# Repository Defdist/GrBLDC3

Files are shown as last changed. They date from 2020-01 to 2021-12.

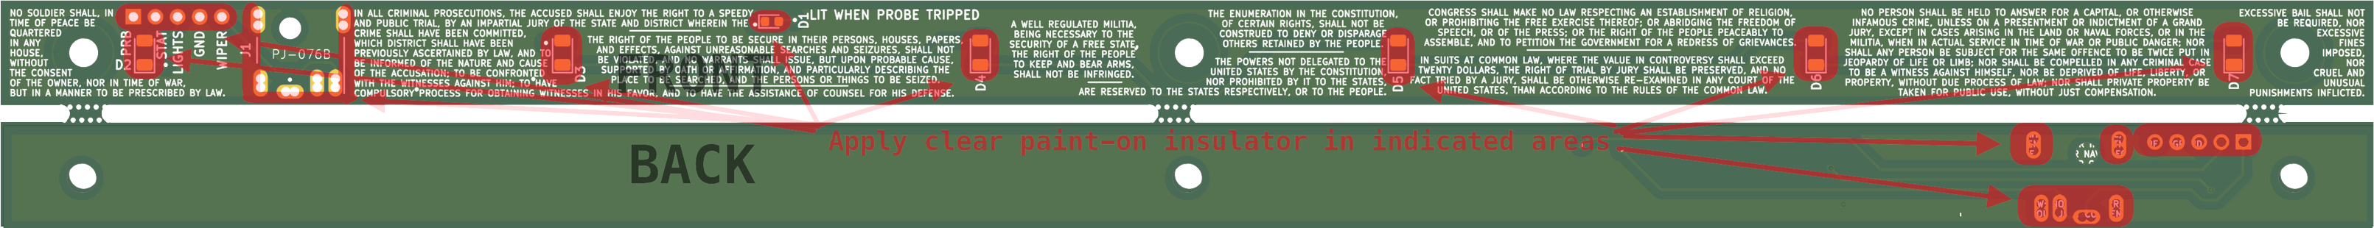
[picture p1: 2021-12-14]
LEDIO PCB/LEDIO 1.2/Areas to Insulate.png

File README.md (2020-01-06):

# GrBLDC3
Uno Shield for grblDD: closed loop spindle VFD + 4 stepper drivers

Main Controller PCB for GG3.  Hardware version 3B
This is the 1st PCB shipped in GG3.

PCB designed in KiCAD.

Changes (from the previous prototype PCB):

-3-pin header order changed from VGS to VSG (e.g. from +-X to +X-).  This creates an incompatibility issue with GG2 units, which will require a pin swap.

-Removed Door Switch (which also restored previous gap for zip tie).

-Vref changed to 1.78 volts (added 1k series with pulldown).

-Added two additional stepper power modes, to reduce power consumption at idle, and to (briefly) increase power if X axis is binding, or if BLDC controller is bogged down in a corner.

-Stepper X1 is now disabled unless A0_STEP_X1_EN is pulled high... this pin is shared with 64M1 reset, which means that when the X1 stepper (only) is disabled, the spindle will not spin.

-Replaced 2x1 screw terminal probe connector with 5x1 SIP.  This is now the only wire harness that goes to LED PCB.  24V and 5V are current limited on this PCB, so that metal chips contacting LED PCB don't affect GrBLDC.

-Added Zener protection diode to 5V rail, in the hope that if 24V finds its way onto that rail, the zener will short it out... this will of course burn out the zener, but hopefully by then the PTC on the Uno will have opened.

-Fixed incorrect pinout on A4910 (pins 39 & 40 swapped).

-BLDC Hall connector changed from 1x5 to 2x3, to make assembling easier.  6th pin is now connected to spindle wipers.

-Removed 2x3 64M1 programming header; connected SPI to Arduino pins instead.  328p can now program this part in-situ (via temporarily loading SPI bitbang firmware onto 328p).

-Emergency stop now pulls BLDC and stepper drivers into reset.

-Emergency stop interface to 328p fixed, such that computer can now pulse reset line during firmware updates.  When estop enabled, 328p continuously held in reset.

-Z stepper connector changed to 2x2, so that it fits through gantry bushings.

-24V/GND/GND 45 degree connector now fits (moved fan connector and capacitors).

New Parts:  
LED PCB:  
102-5777-ND  
Get longer right angle SIPs for LED PCB  
LED - 732-5660-1-ND

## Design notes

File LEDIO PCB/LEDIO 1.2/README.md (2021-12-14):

# LEDIO
LED PCB for GG3.

PCB designed in KiCAD.

Changes (from the previous PCB):

Added fiducials for P&P Camera

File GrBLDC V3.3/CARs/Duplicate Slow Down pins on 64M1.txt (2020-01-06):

Pins PC3 (64M1:7) AND PD4 (64M1:12) perform the same function: tell 328p when to slow down.  This doesn't require a board spin, but if the board is ever modified and more pins are needed, then we can repurpose PC3 (NOT PD4).  PD4 must remain connected because it is the 64M1's SPI programming clock pin.

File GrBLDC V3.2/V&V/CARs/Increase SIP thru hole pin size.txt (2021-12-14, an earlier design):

The thru holes for several SIPs are too small... hard to insert pins.

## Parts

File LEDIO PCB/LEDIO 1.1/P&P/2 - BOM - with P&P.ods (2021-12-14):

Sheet: SMT P&P (ONLY)
Note: This is the master page. The next tab should have columns A:J copy-pasted to create csv file
# | Nozzle | Reel | X p&p | Y p&p | Rot p&p | Height | Skip | Ref | Note | Package | Val | X kicad | Y kicad | Rot kicad | Note | Digikey PN | $@QTY | QTY/GG | QTY in 700 GG3s | nominal $ per GG3 | Leftover QTY from GG2 | QTY needed for 700 GG3s | purchased in multiples of | QTY to buy in 1st order | $ (total)
 |  |  |  |  |  |  |  |  |  |  |  |  |  |  |  |  |  |  | $(nom)/PCB | #REF!

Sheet: Hand Place (ONLY)
Description | Note | Digikey PN | $@QTY | QTY/GG | QTY in 700 GG3s | nominal $ per GG3 | Leftover QTY from GG2 | QTY needed for 700 GG3s | purchased in multiples of | QTY to buy in 1st order | $ (total) in 1st order
Barrel Jack |  | PJ-076B | 0.5808 | 1 | 700 | 0.58 | 0 | 700 | 1000 | 1000 | 580.8
Barrel Connector | Technically part of probe cable, but included here | CP3-1001-ND | 0.7136 | 1 | 700 | 0.71 | 0 | 700 | 1000 | 1000 | 713.6
Right angle conn | 0.015 uin min gold plating, 8 to 9 mm length | WM50026-05-ND | 0.2520 | 1 | 700 | 0.25 | 0 | 700 | 500 | 700 | 176.37
LED - green | Right angle | 160-1478-1-ND | 0.0432 | 1 | 700 | 0.04 | 0 | 700 | 4000 | 4000 | 172.96
LED - white |  | 732-5660-2-ND | 0.1330 | 6 | 4200 | 0.8 | 6000 | -1800 | 2000 | 0 | 0
LED PCB | The actual PCB | - | 0.5400 | 1 | 700 | 0.54 | 0 | 700 | 500 | 1000 | 540
 |  |  |  |  | $(nom)/PCB | 2.93

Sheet: FULL BOM EXPORT
Part | Note | Digikey PN | $@QTY | QTY /GG | QTY in 700 GG3s | nominal $ per GG3 | Leftover GG2 QTY | QTY needed for 700 GG3s | purchased in multiples of | Recommended QTY to buy in 1st order | $ for 1st order
 |  |  |  |  | nominal $ per GG3 | #REF!

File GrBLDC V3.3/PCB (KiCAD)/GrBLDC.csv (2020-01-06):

Id | Designator | Package | Quantity | Designation | Supplier and ref
1 | Fiducial,Fiducial,Fiducial | Fiducial | 3 | VAL**
2 | C6,C36,C37,C29,C21,C35,C38,C48,C49,C50,C51,C53,C52,C44 | SM1206 | 14 | 10u
3 | C7,C25,C20,C16,C24,C5,C3,C4 | SM0805 | 8 | 1u
4 | R32,R29,R31,R34,R33,R30 | SM0603 | 6 | 470k
5 | R28,R27,R26,R25,R24,R23,R51,R52 | SM0603 | 8 | 47
6 | C2,C28,C22,C19,C26,C23,C14,C10,C11,C8,C12,C9,C15,C1,C17,C27,C34,C39,C18,C42,C13 | SM0603 | 21 | 220n
7 | R2,R1,R4,R47,R45,R44,R42 | SM0603 | 7 | 470
8 | C31,C32,C30 | SM0603 | 3 | 33n
9 | R20,R5,R6,R18,R19,R21,R7,R37 | SM0603 | 8 | 40.2k
10 | R16,R13,R14,R10,R15,R11,R12,R8,R9,R3,R22,R36,R35,R43,R46,R48,R50 | SM0603 | 17 | 1k
11 | P5 | SIL-9 | 1 | CONN_9
12 | P10,P2,P6,P9,P7,P4 | SIL-8 | 6 | CONN_8
13 | P1 | SIL-6 | 1 | CONN_6
14 | JP1 | SIL-3 | 1 | JUMPER3
15 | P11 | SIL-2 | 1 | CONN_2
16 | P12 | Conn_1751280 | 1 | CONN_6
17 | C33,C46,C43 | Cap_Nichicon_UCL1V331MNL1GS | 3 | 330u
18 | C45,C47 | Cap_Nichicon_UCL1V331MNL1GS | 2 | 220u
19 | U1 | A4915 | 1 | A4915-JTS
20 | P8,P3 | Conn_1751303 | 2 | CONN_8
21 | ILTC1 | ILTC | 1 | ILTC
22 | R17,R40 | SM0603 | 2 | SPARE
23 | VAL | DDsmall | 1 | REF
24 | U4 | SOT23-5 | 1 | LT1797
25 | U3,U2 | SOT23-5 | 2 | MCP6561
26 | D1 | SOT23 | 1 | LM4040
27 | R49 | SM1206 | 1 | 0.010
28 | C41 | SM1206 | 1 | 82n
29 | R39,R38,R41 | SM0603 | 3 | 40.2K
30 | C40 | SM0603 | 1 | 2n
31 | RV1 | POT_3361 | 1 | POT
32 | Q5,Q4,Q6,Q3,Q2,Q1 | IRF5406 | 6 | IRF5406

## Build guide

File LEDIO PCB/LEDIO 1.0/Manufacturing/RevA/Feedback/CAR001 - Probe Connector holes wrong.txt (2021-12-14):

DC Power jack connector PTH incorrect... jack leads don't fit through (round) hole.
Headphone jack connector PTH incorrect... jack leads don't fit through (round) hole.

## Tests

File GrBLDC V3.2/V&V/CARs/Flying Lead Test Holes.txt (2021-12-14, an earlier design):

Need to add flying lead test holes so that Seeedstudio doesn't blow holes through planes in bad places.

Seeed recommends:
1.5 mm min, preferably 2 mm
one hole on each corner
Fixture testing (large batches) requires board margins

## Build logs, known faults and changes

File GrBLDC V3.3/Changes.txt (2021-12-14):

RevC Changes:

-Added QTY4 mechanical thru holes for flying probe tester
-Added D4 to prevent sinking into the 24 volt rail.  PN is SMZJ3800B-E3/52GITR-ND
-Changed Thru hole ID on P1/P2/P8/P9/P10/P11 from 0.813 mm to 1.000 mm
-Moved C51/C55/C56/C59/C60 to make room for D4.

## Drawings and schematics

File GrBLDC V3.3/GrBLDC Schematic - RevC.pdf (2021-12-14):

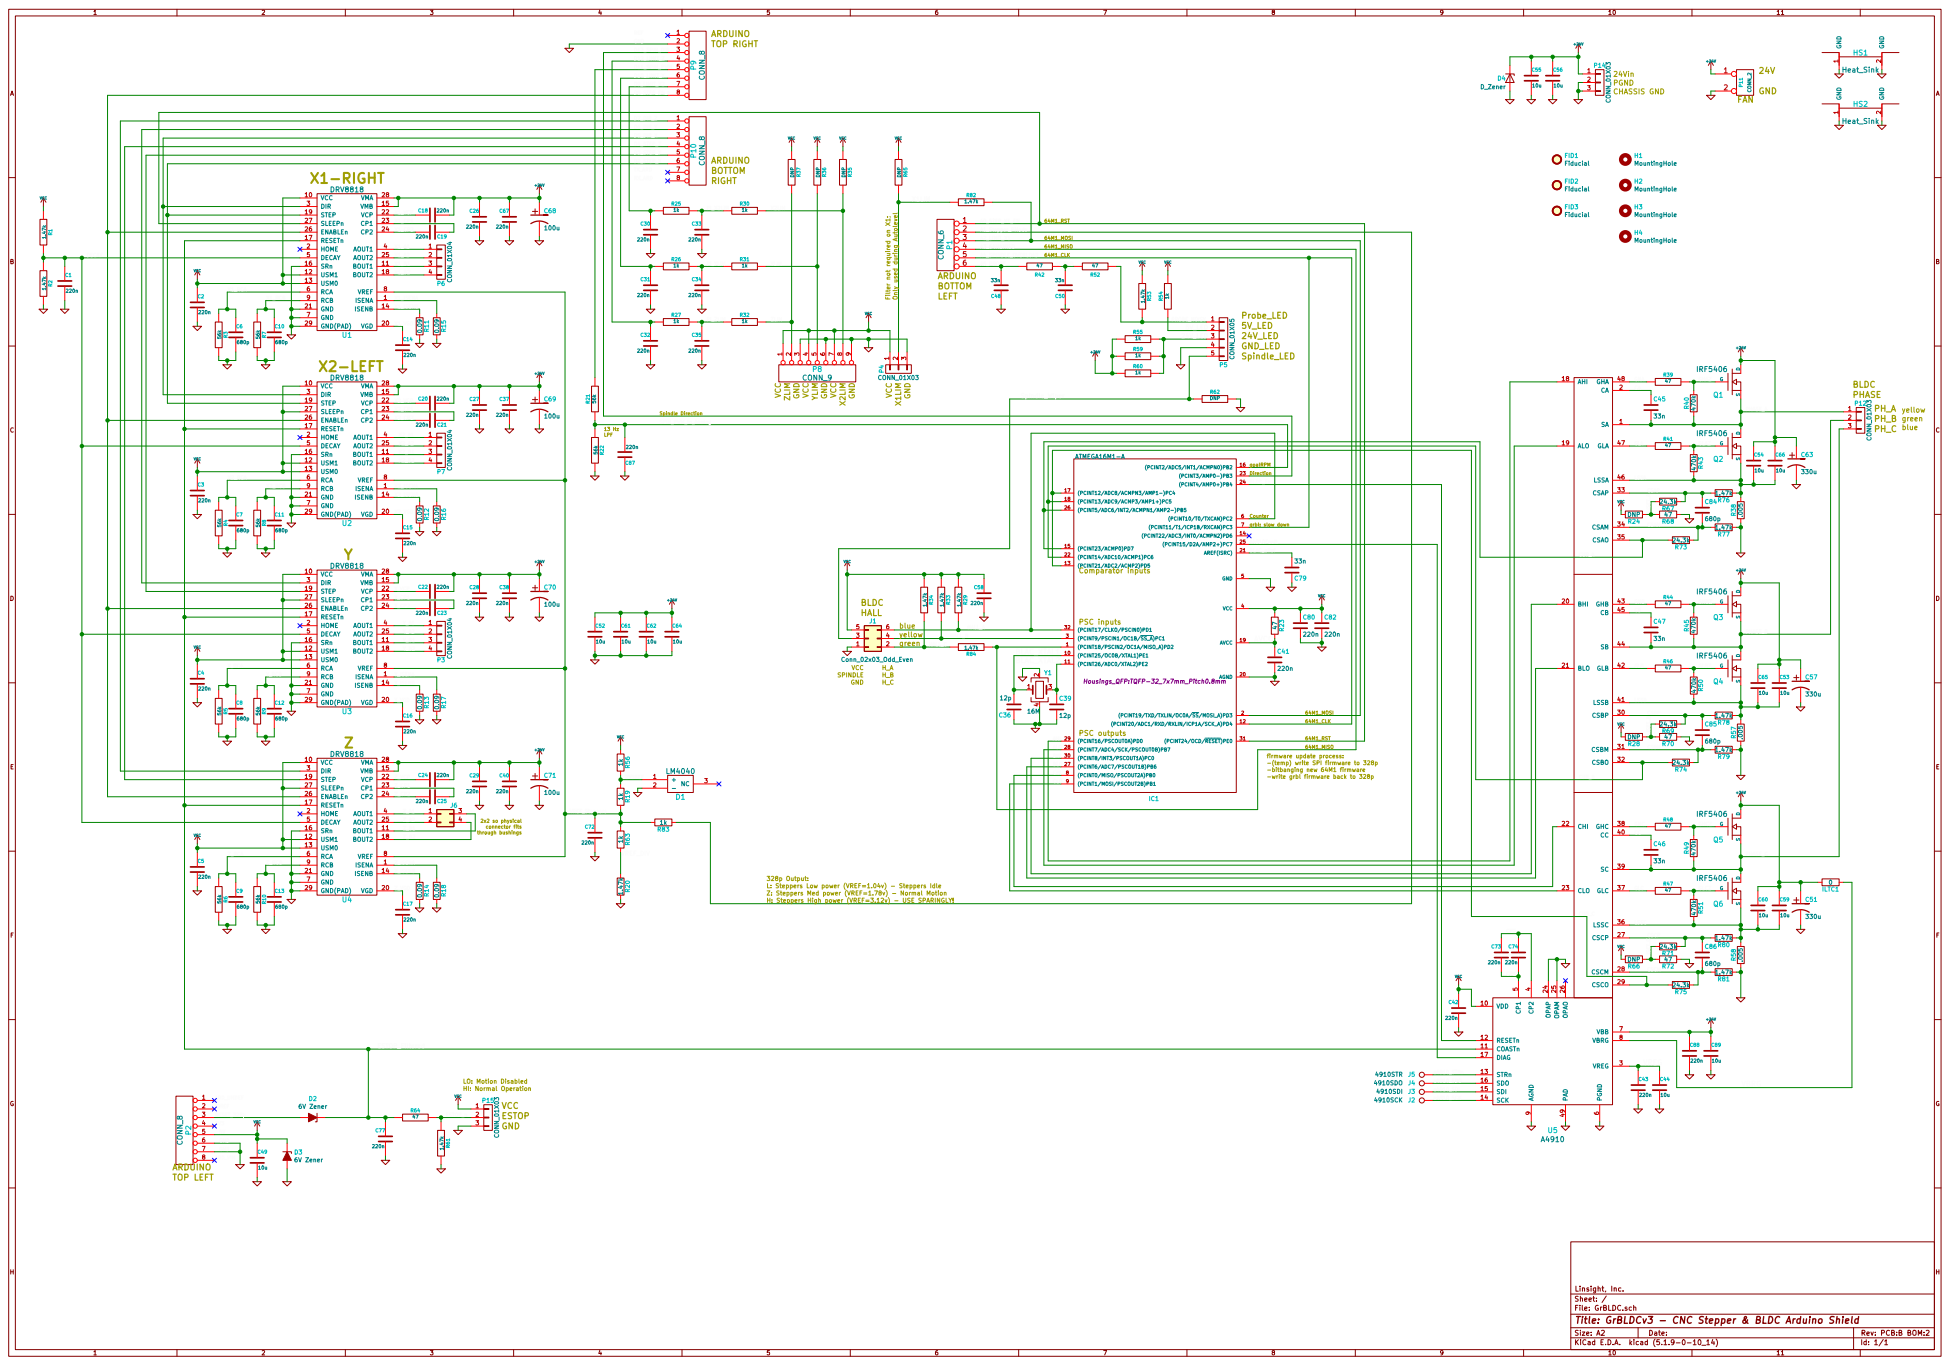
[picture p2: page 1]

goalRPM VCC ZLIM GND VCC YLIM GND VCC X2LIM GND

firmware update process:
-(temp) write SPI firmware to 328p -bitbanging new 64M1 firmware

-write grbl firmware back to 328p

2x2 so physical connector fits

328p Output:
L: Steppers Low power (VREF=1.04v) - Steppers Idle
Z: Steppers Med power (VREF=1.78v) - Normal Motion
H: Steppers High power (VREF=3.12v) - USE SPARINGLY!

File: GrBLDC.sch Sheet: / Linsight, Inc.

Id: 1/1 Title: GrBLDCv3 - CNC Stepper & BLDC Arduino Shield

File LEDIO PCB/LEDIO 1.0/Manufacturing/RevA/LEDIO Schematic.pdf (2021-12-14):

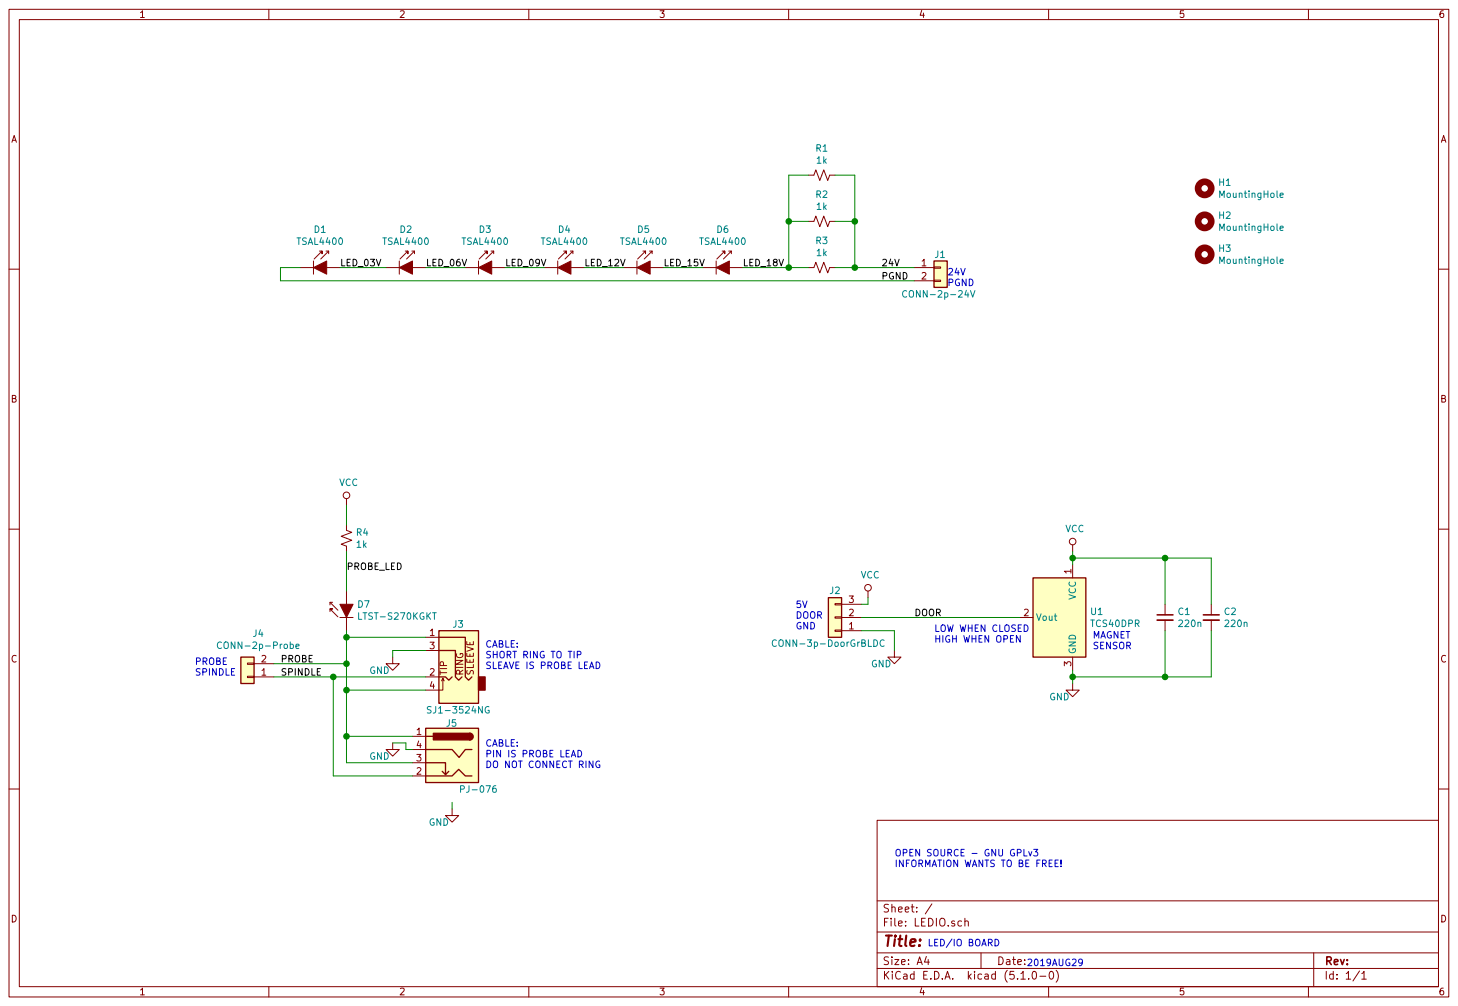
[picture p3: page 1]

J2 CONN-3p-DoorGrBLDC TIP RING SLEEVE

DOOR
INFORMATION WANTS TO BE FREE! LOW WHEN CLOSED

SLEAVE IS PROBE LEAD

CABLE: PIN IS PROBE LEAD

DO NOT CONNECT RING

LED/IO BOARD OPEN SOURCE - GNU GPLv3

Id: 1/1 Title: File: LEDIO.sch Sheet: /

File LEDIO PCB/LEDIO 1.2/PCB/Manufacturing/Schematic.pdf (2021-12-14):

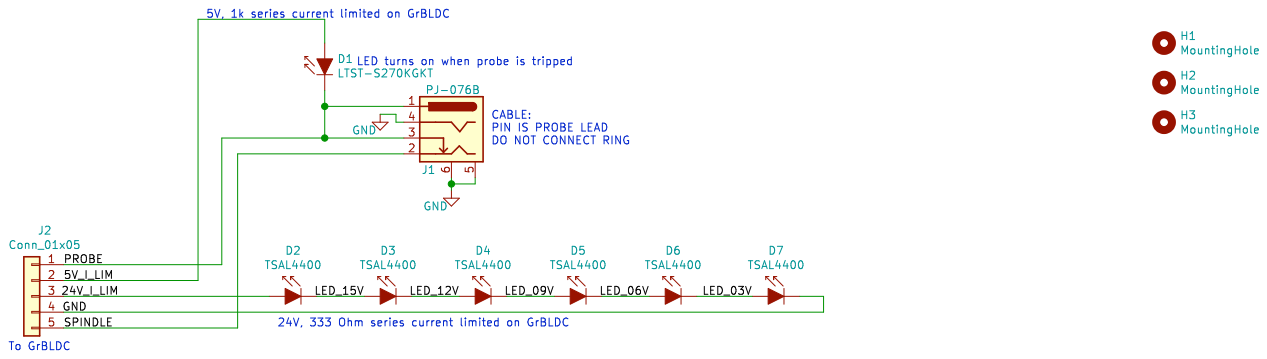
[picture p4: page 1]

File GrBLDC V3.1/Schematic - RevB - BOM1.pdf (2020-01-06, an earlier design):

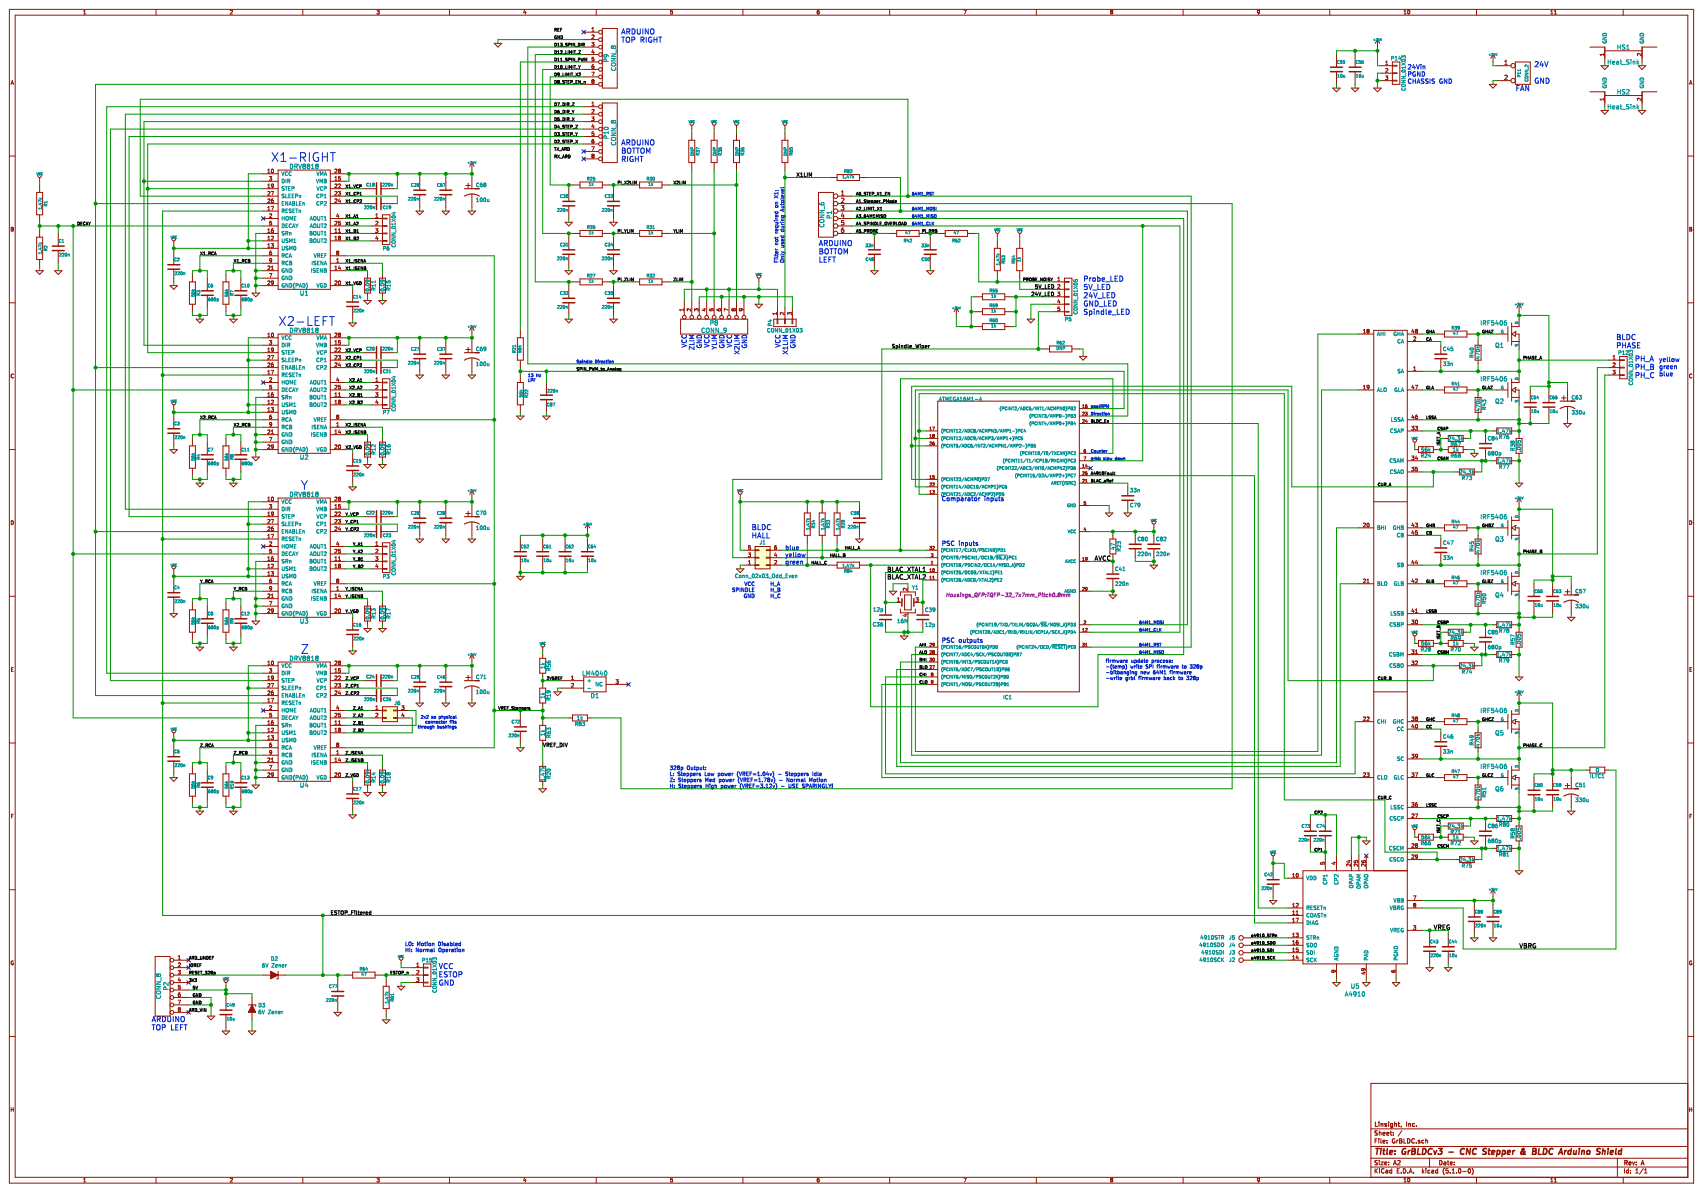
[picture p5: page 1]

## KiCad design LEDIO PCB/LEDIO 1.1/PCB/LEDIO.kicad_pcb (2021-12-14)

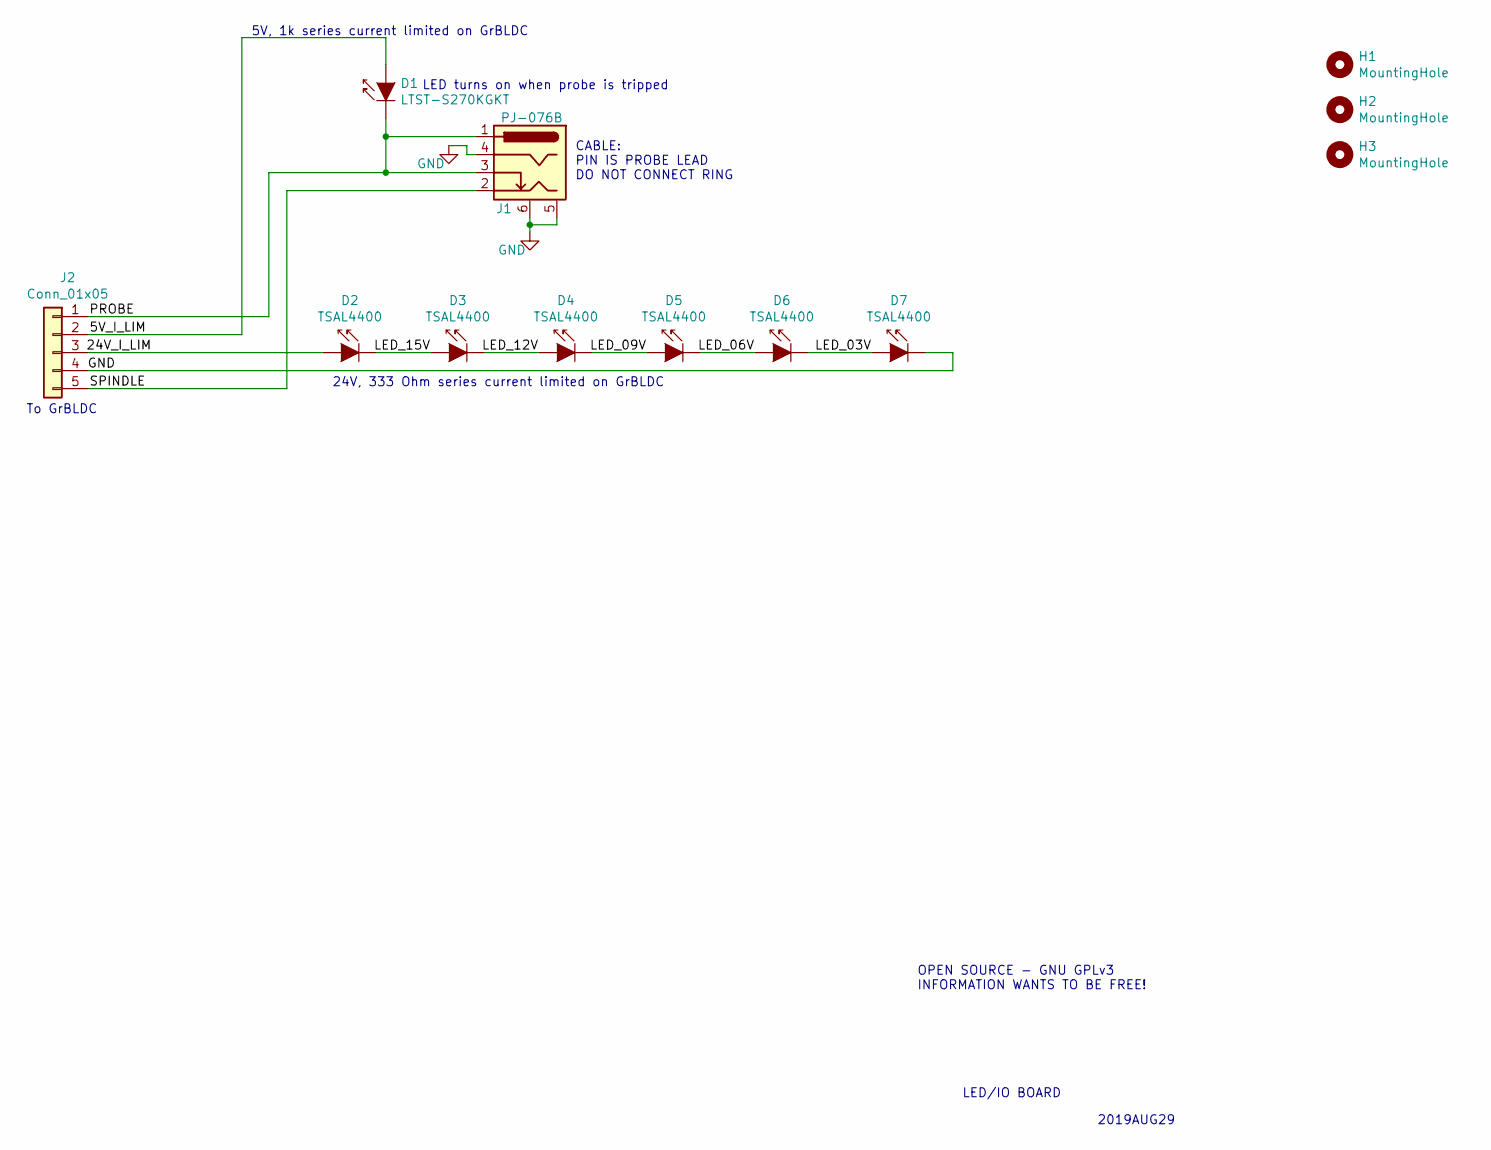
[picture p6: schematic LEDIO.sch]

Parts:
D1: LTST-S270KGKT; D_0603_1608Metric
D2, D3, D4, D5, D6, D7: TSAL4400; D_1206_3216Metric
H1, H2, H3: MountingHole; MountingHole_3.2mm_M3
J1: PJ-076B; CUI_PJ-076
J2: Conn_01x05; PinHeader_1x05_P2.54mm_Horizontal

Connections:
/5V_I_LIM: D1.2 (A), J2.2
/24V_I_LIM: D2.2 (A), J2.3
/LED_03V: D6.1 (K), D7.2 (A)
/LED_06V: D5.1 (K), D6.2 (A)
/LED_09V: D4.1 (K), D5.2 (A)
/LED_12V: D3.1 (K), D4.2 (A)
/LED_15V: D2.1 (K), D3.2 (A)
/PROBE: D1.1 (K), J1.1, J1.3, J2.1
/SPINDLE: J1.2, J2.5
GND: D7.1 (K), J1.4, J1.5 (ShieldA), J1.6 (ShieldB), J2.4

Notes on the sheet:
CABLE: PIN IS PROBE LEAD DO NOT CONNECT RING
2019AUG29
LED/IO BOARD
OPEN SOURCE - GNU GPLv3 INFORMATION WANTS TO BE FREE!
5V, 1k series current limited on GrBLDC
To GrBLDC
LED turns on when probe is tripped
24V, 333 Ohm series current limited on GrBLDC

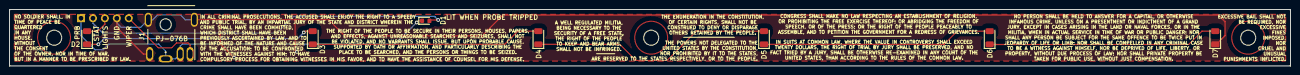
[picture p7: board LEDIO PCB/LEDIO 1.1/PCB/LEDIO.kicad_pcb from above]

Board: 2 copper layers, 272.5 x 12.0 mm, 12 parts (1 on the bottom side), 10 nets.

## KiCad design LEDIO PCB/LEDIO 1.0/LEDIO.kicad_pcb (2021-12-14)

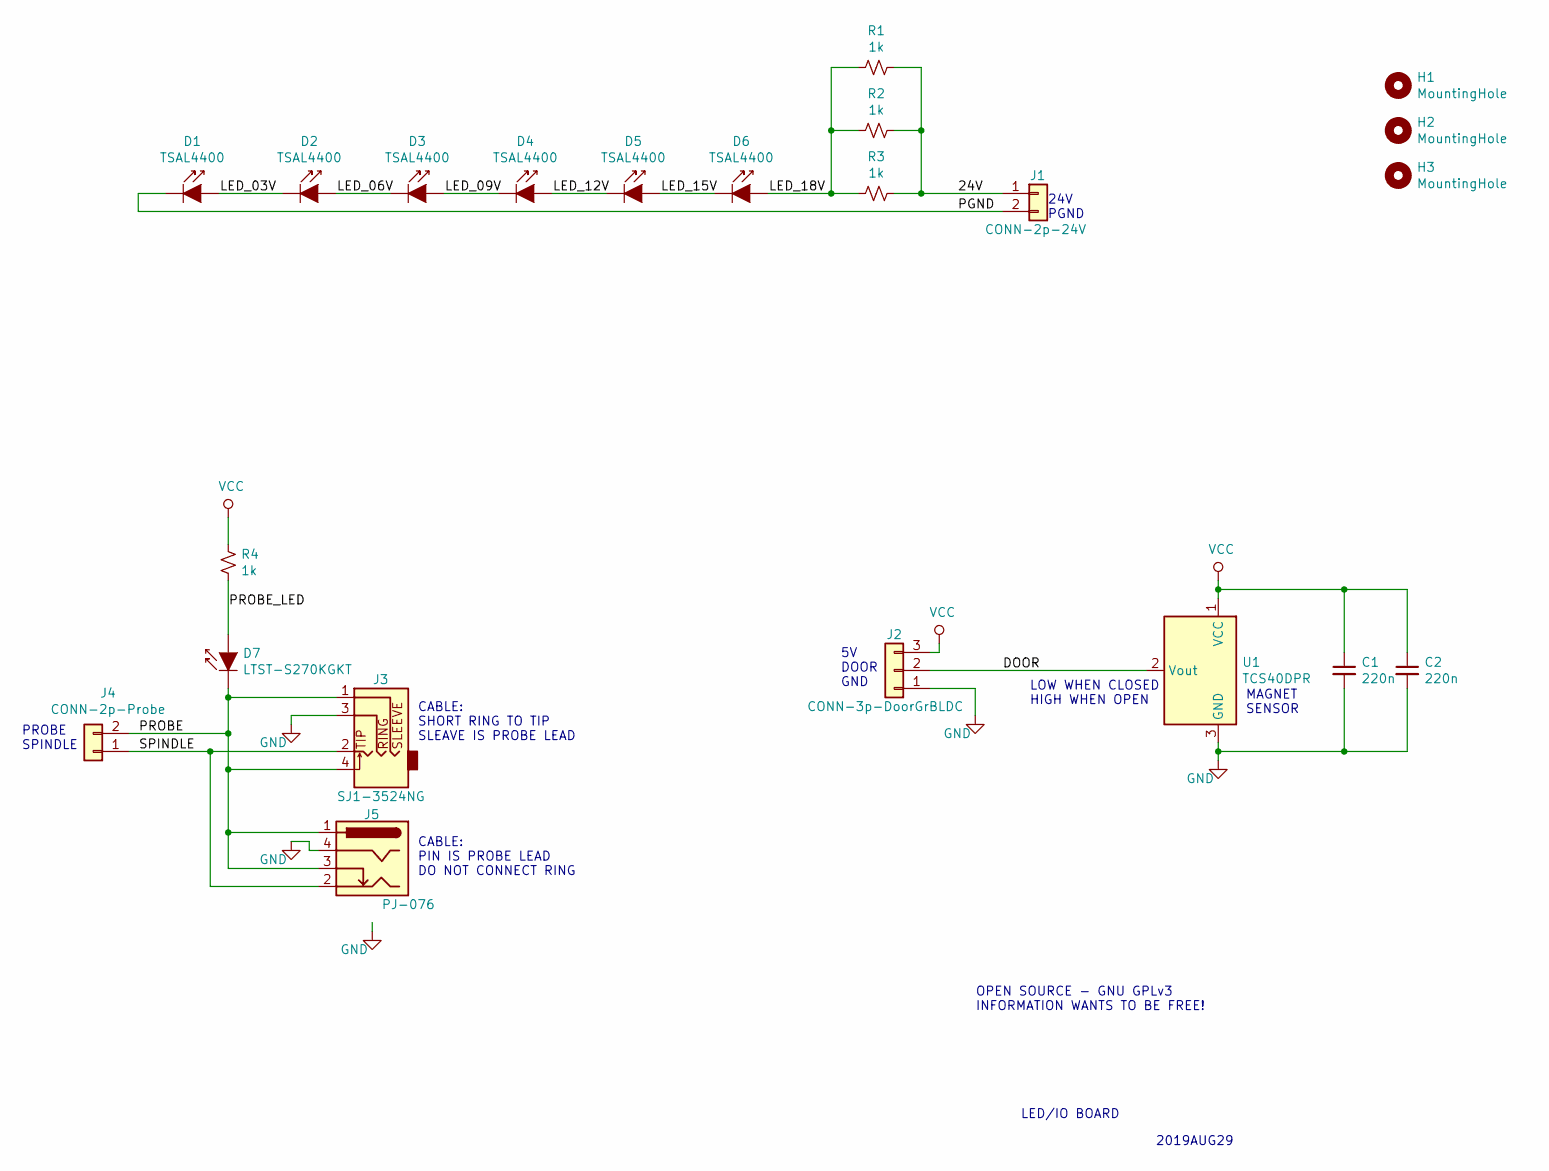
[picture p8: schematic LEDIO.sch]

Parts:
C1, C2: 220n; C_0603_1608Metric
D1, D2, D3, D4, D5, D6: TSAL4400; D_1206_3216Metric
D7: LTST-S270KGKT; D_0603_1608Metric
H1, H2, H3: MountingHole; MountingHole_3.2mm_M3
J1: CONN-2p-24V; PinHeader_1x02_P2.54mm_Horizontal
J2: CONN-3p-DoorGrBLDC; PinHeader_1x03_P2.54mm_Horizontal
J3: SJ1-3524NG; CUI_SJ1-3524NG
J4: CONN-2p-Probe; PinHeader_1x02_P2.54mm_Horizontal
J5: PJ-076; CUI_PJ-076
R1, R2, R3, R4: 1k; R_0603_1608Metric
U1: TCS40DPR; SOT-23

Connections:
/24V: J1.1, R1.1, R2.1, R3.1
/DOOR: J2.2, U1.2 (Vout)
/LED_03V: D1.2 (A), D2.1 (K)
/LED_06V: D2.2 (A), D3.1 (K)
/LED_09V: D3.2 (A), D4.1 (K)
/LED_12V: D4.2 (A), D5.1 (K)
/LED_15V: D5.2 (A), D6.1 (K)
/LED_18V: D6.2 (A), R1.2, R2.2, R3.2
/PGND: D1.1 (K), J1.2
/PROBE: D7.1 (K), J3.1, J3.4, J4.2, J5.1, J5.3
/PROBE_LED: D7.2 (A), R4.2
/SPINDLE: J3.2, J4.1, J5.2
GND: C1.2, C2.2, J2.1, J3.3, J5.4, U1.3 (GND)
VCC: C1.1, C2.1, J2.3, R4.1, U1.1 (VCC)

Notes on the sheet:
24V PGND
5V DOOR GND
PROBE SPINDLE
CABLE: SHORT RING TO TIP SLEAVE IS PROBE LEAD
CABLE: PIN IS PROBE LEAD DO NOT CONNECT RING
MAGNET SENSOR
2019AUG29
LED/IO BOARD
OPEN SOURCE - GNU GPLv3 INFORMATION WANTS TO BE FREE!
LOW WHEN CLOSED HIGH WHEN OPEN

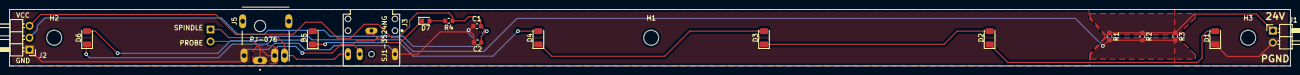
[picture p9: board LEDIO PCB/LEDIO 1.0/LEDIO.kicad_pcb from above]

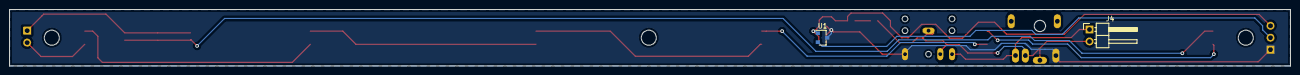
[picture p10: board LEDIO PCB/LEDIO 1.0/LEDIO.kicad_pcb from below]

Board: 2 copper layers, 272.5 x 12.0 mm, 22 parts (2 on the bottom side), 14 nets.

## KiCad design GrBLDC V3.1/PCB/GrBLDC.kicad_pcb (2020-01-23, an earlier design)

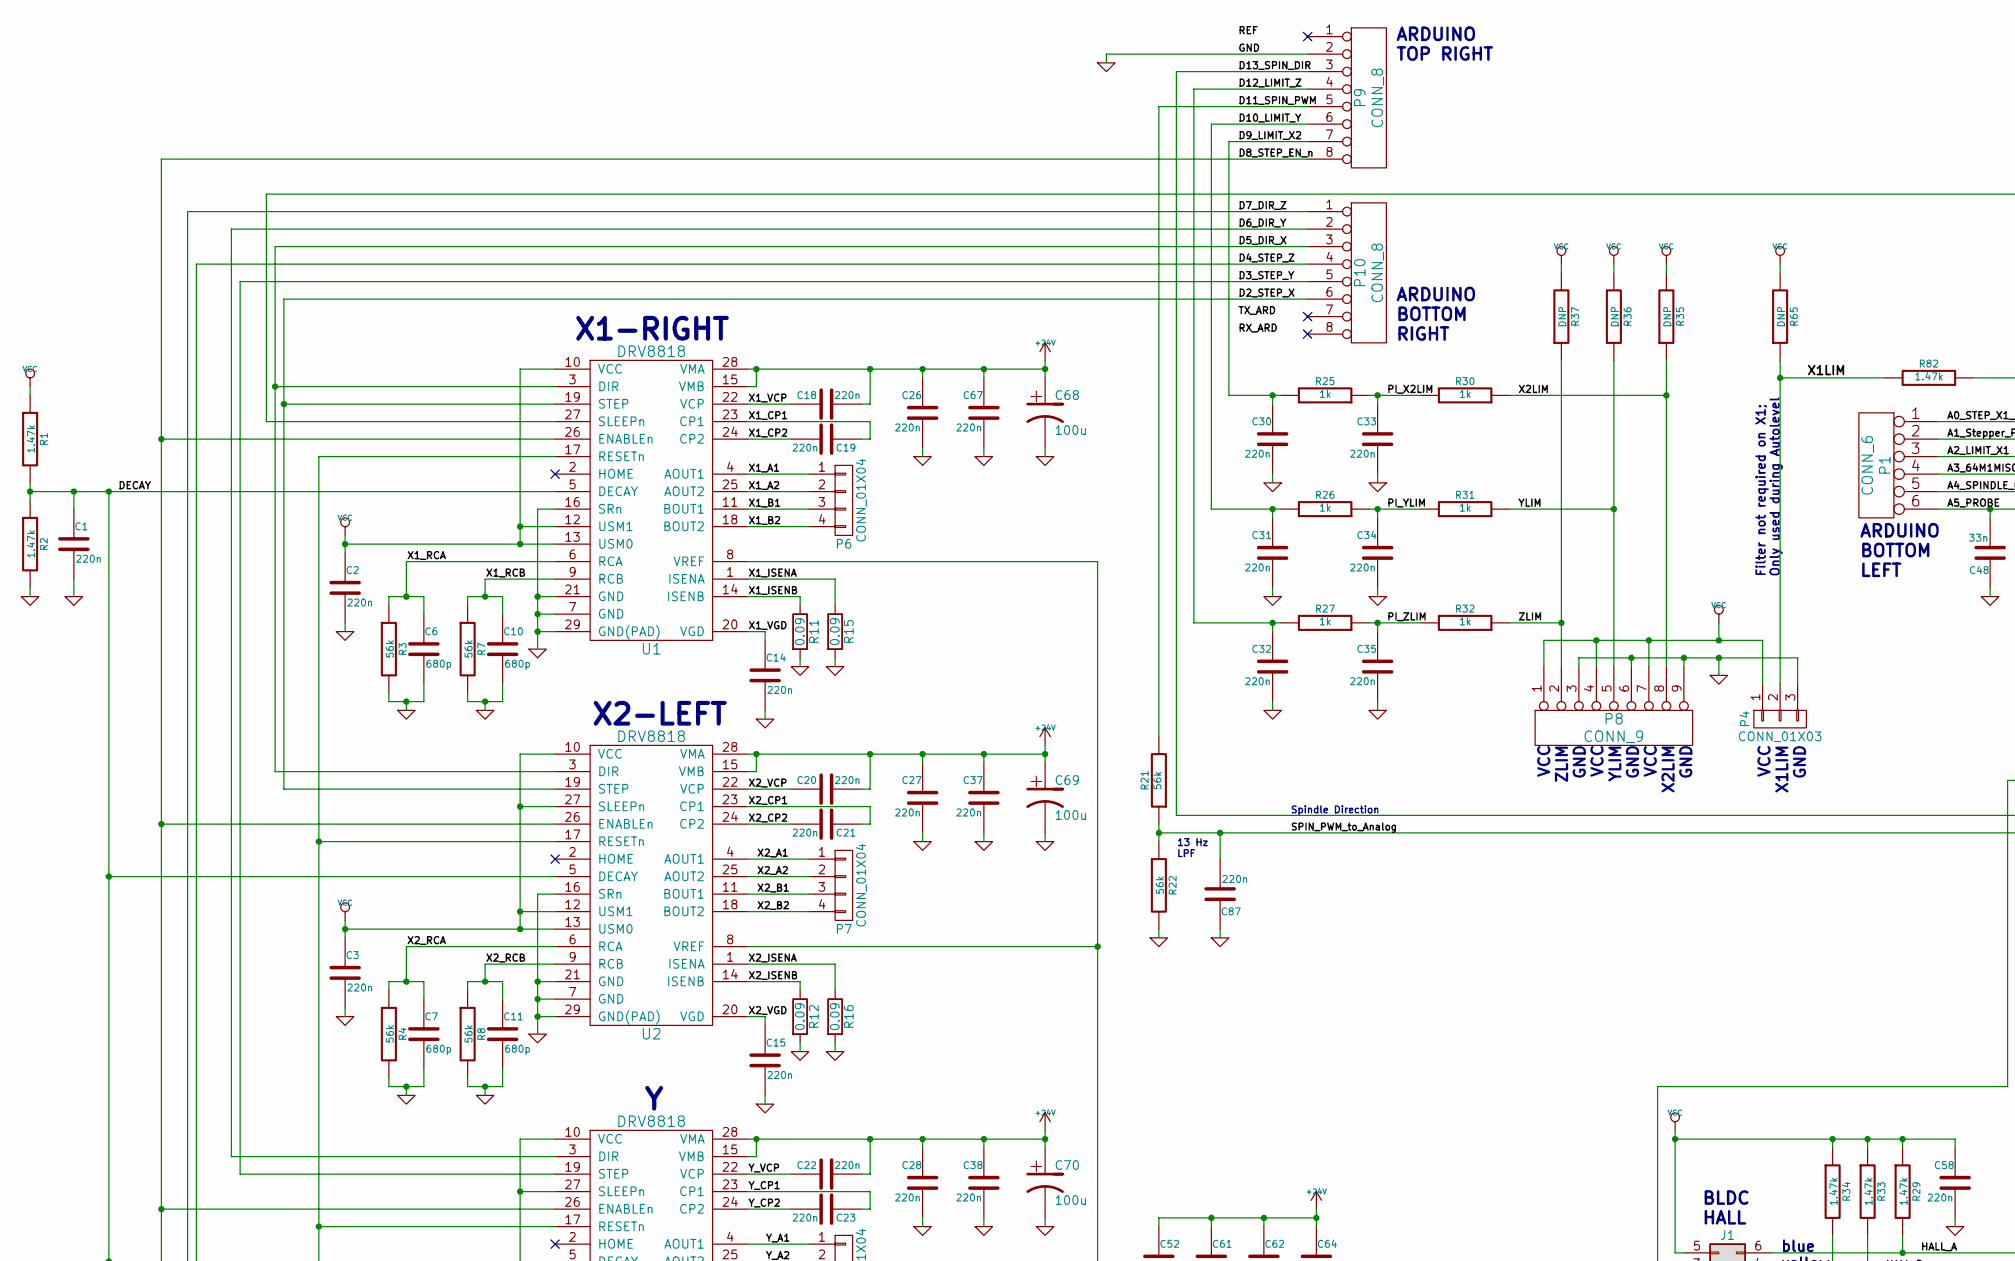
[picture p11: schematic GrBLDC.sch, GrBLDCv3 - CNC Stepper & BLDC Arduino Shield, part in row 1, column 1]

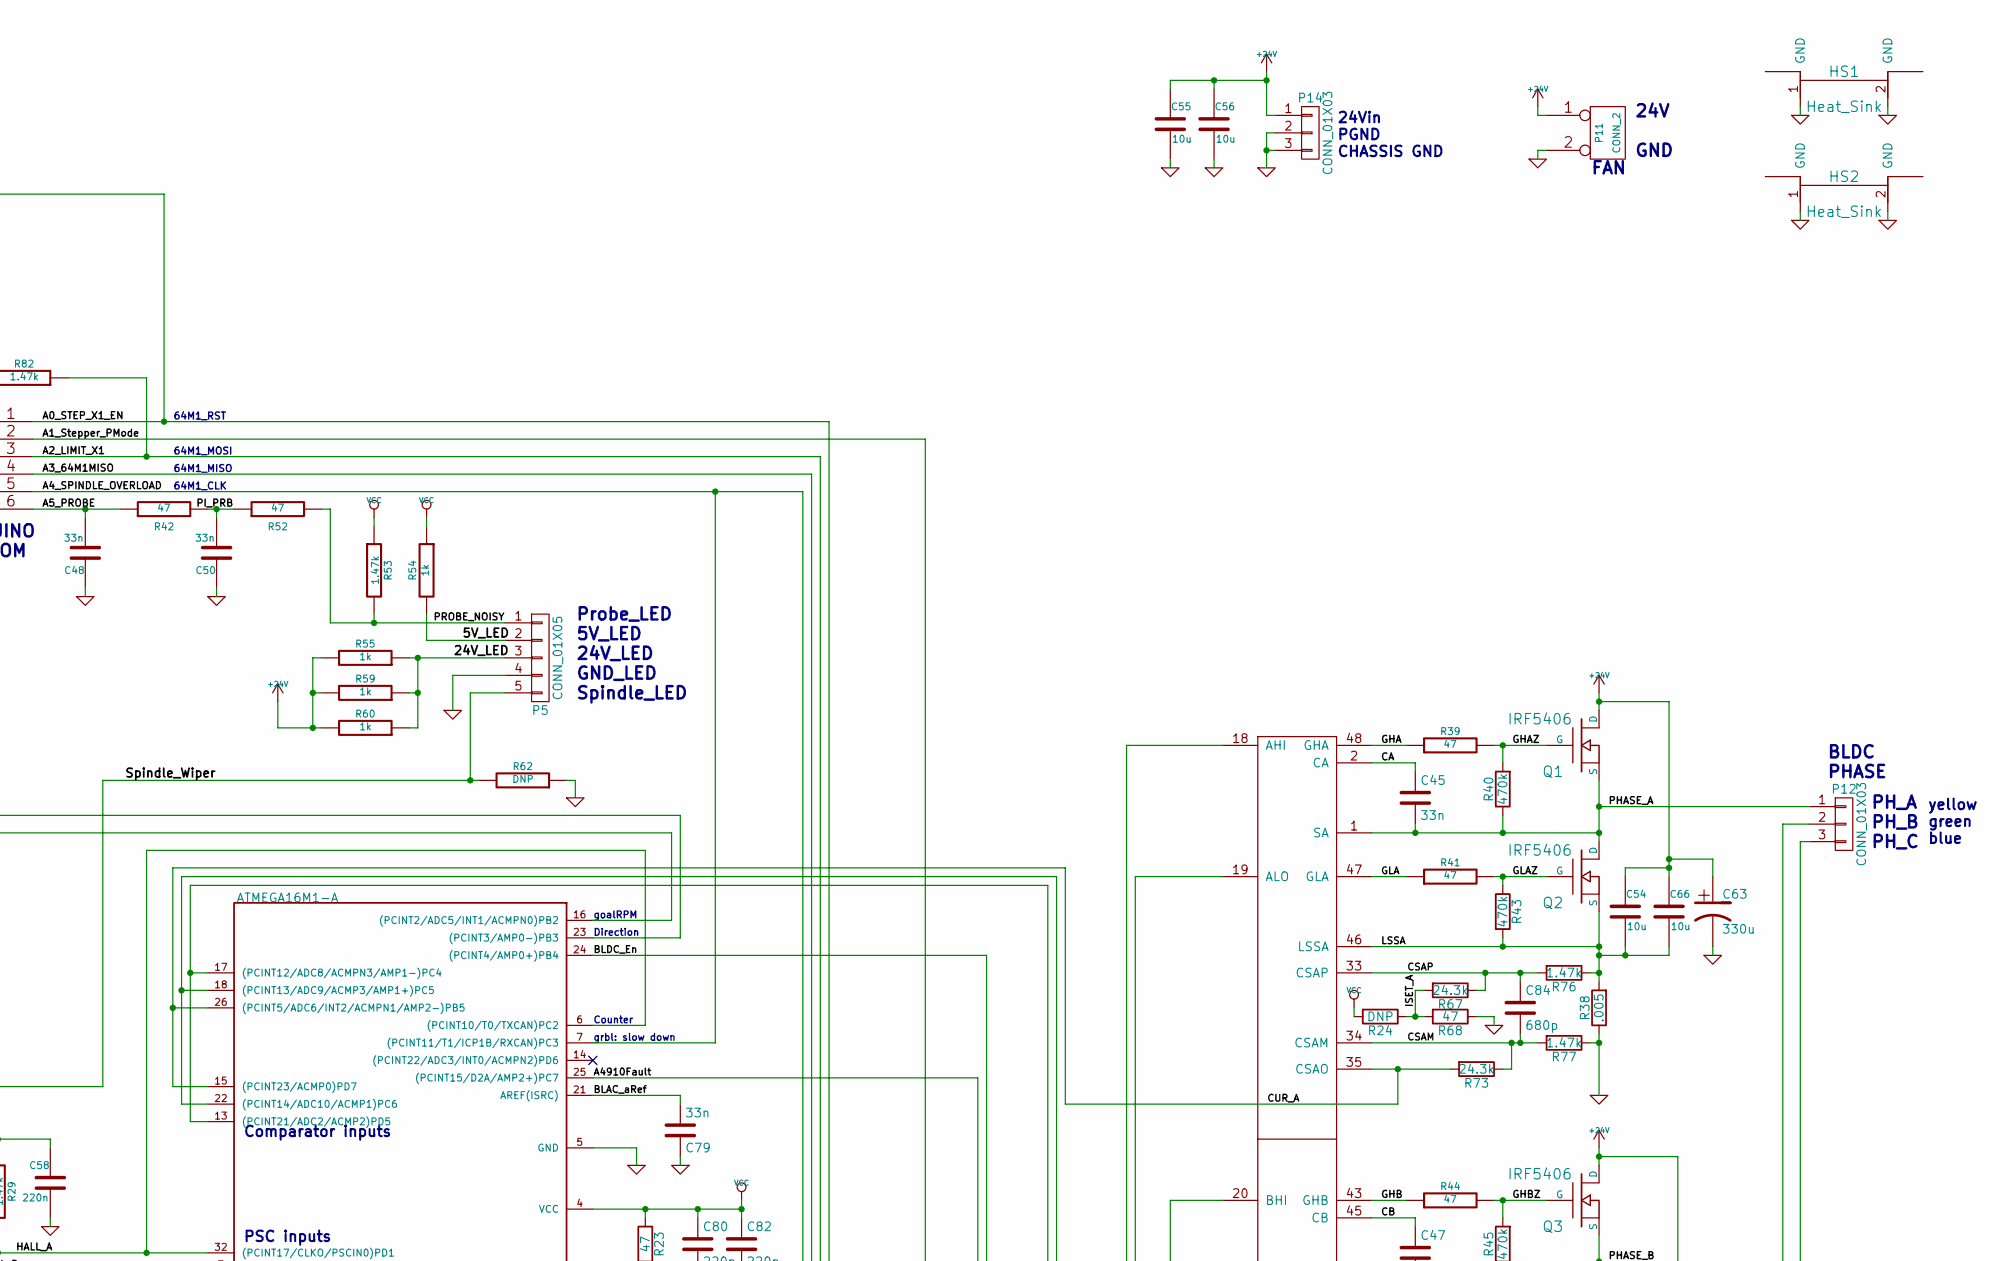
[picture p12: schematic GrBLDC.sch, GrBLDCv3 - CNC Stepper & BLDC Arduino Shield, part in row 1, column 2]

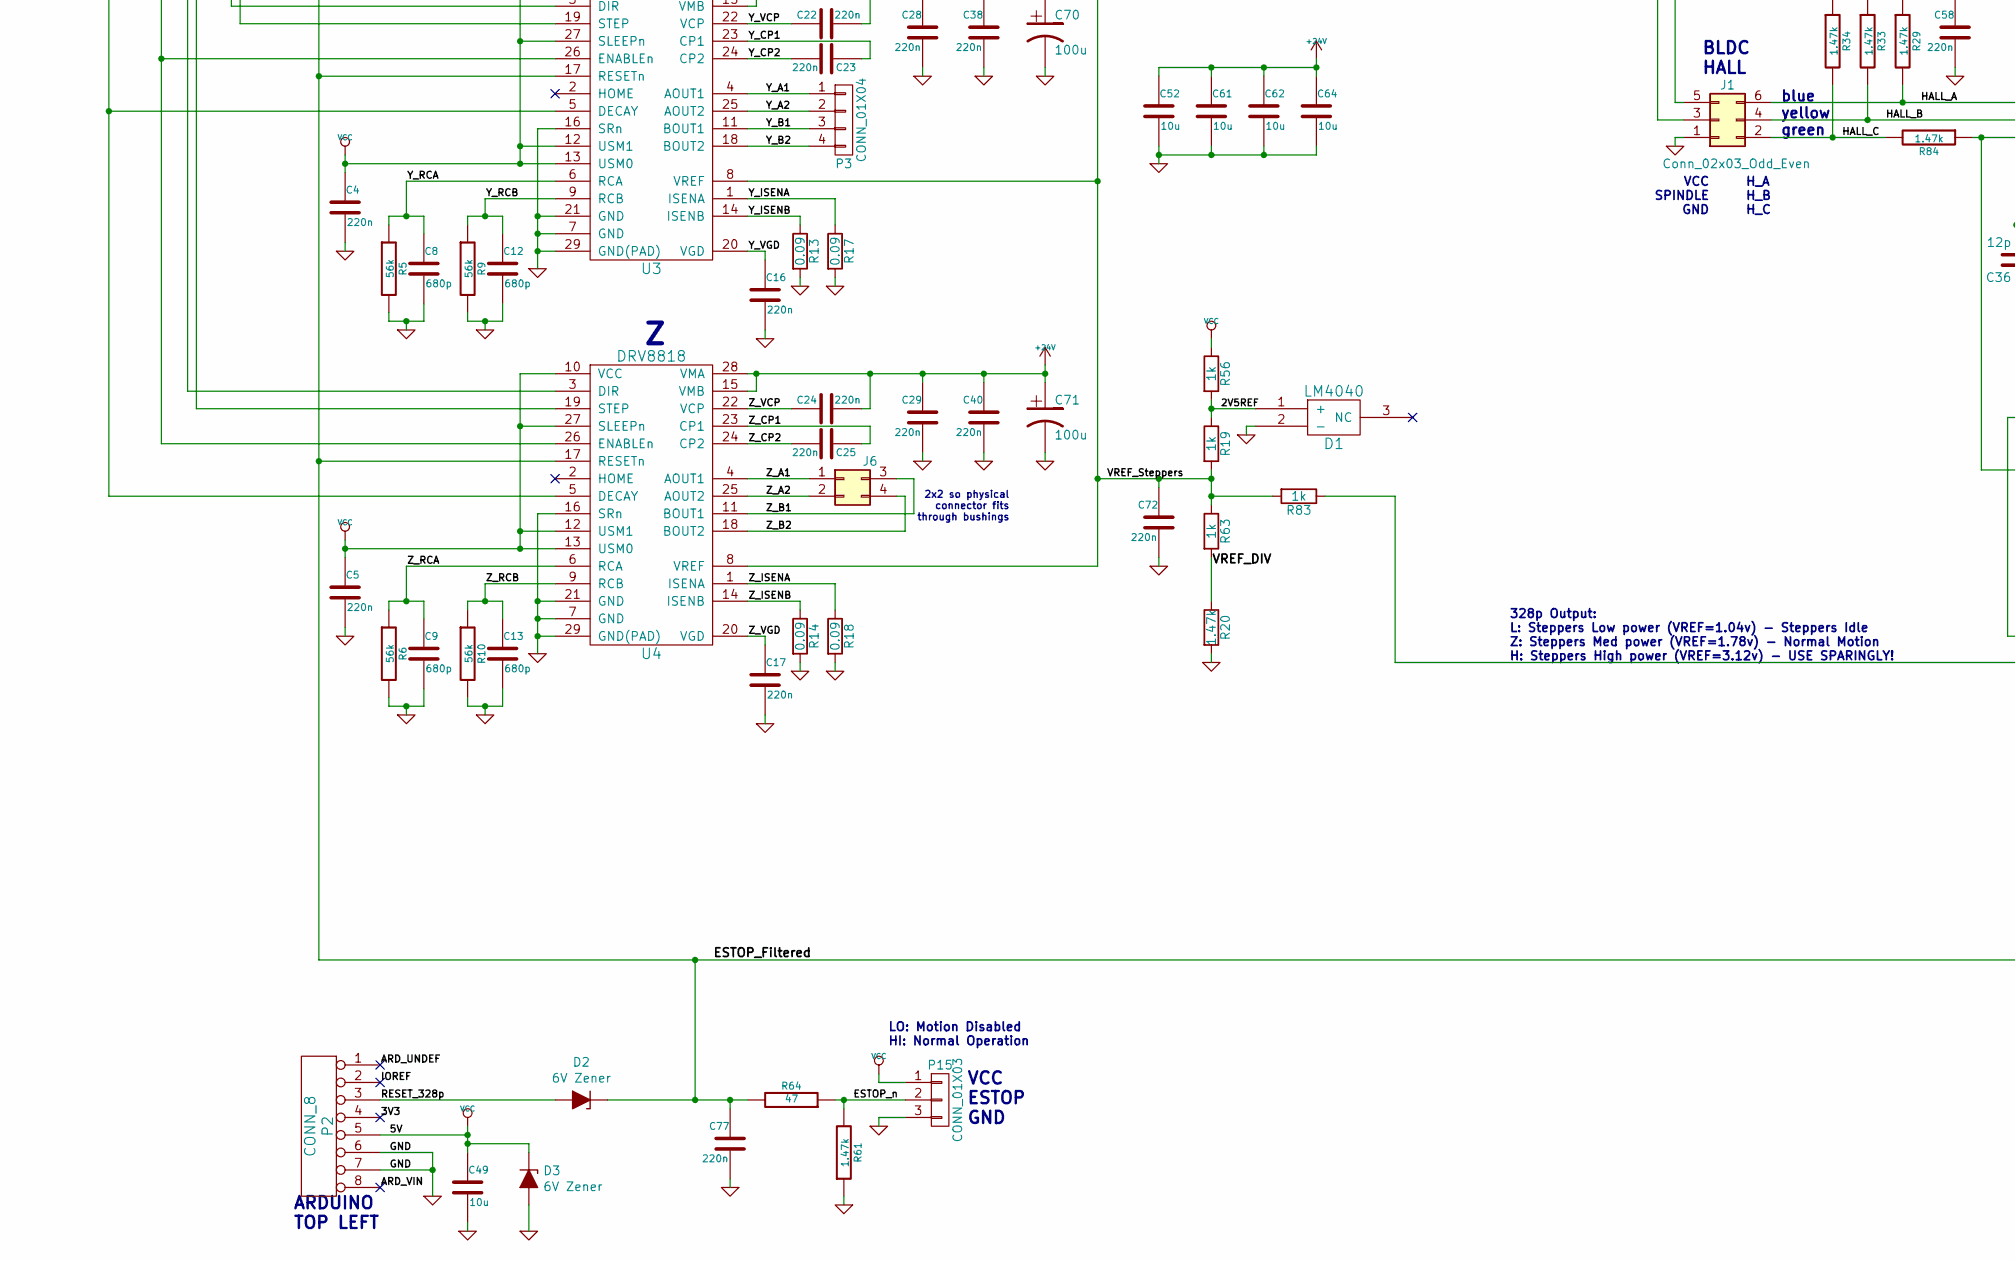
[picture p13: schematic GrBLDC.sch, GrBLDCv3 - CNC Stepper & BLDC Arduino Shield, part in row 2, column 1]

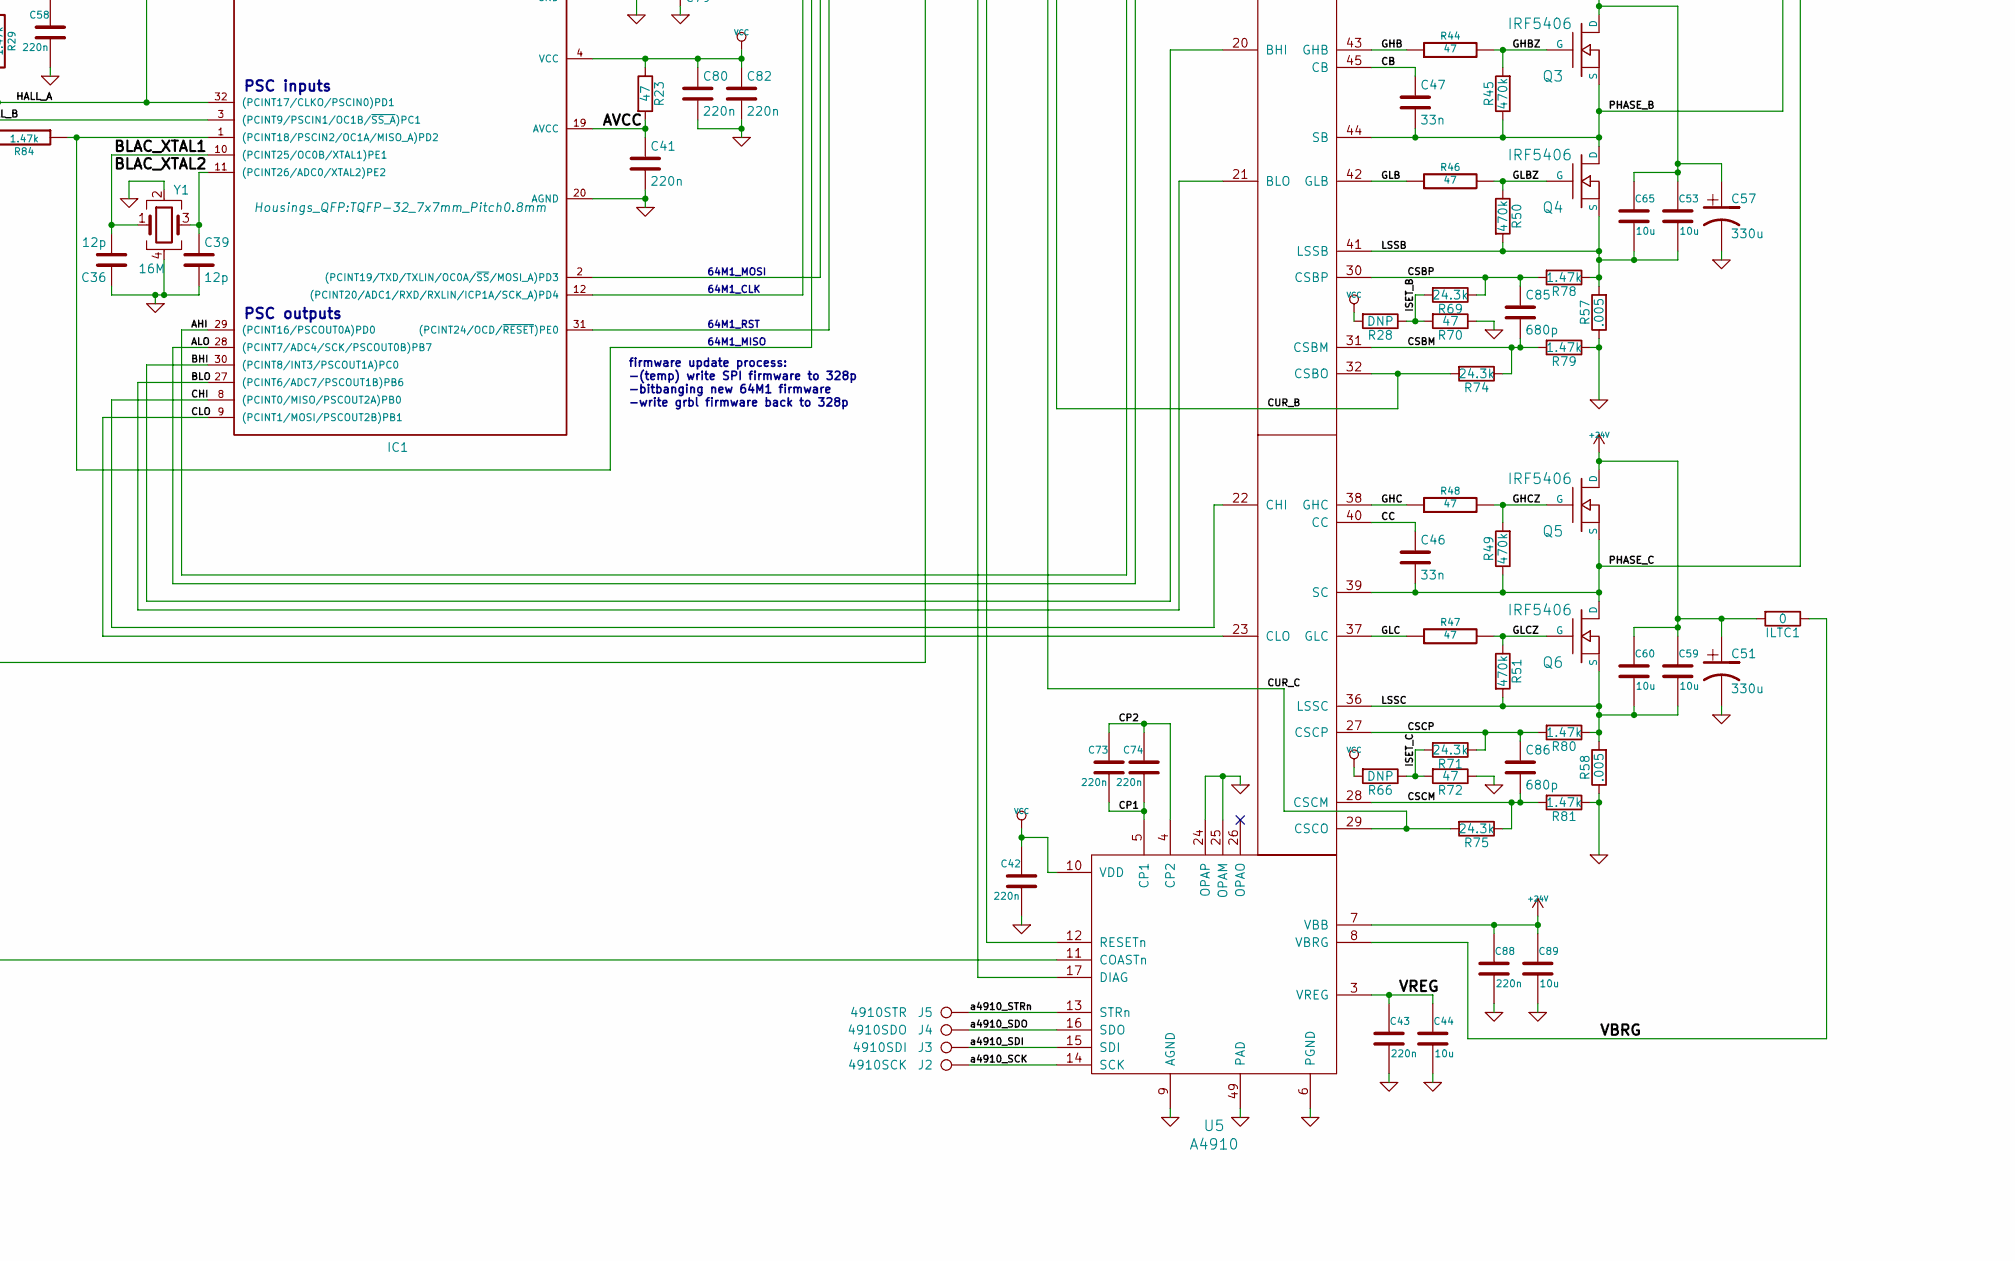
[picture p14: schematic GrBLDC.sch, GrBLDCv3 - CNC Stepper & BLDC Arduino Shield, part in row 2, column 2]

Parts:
C1, C2, C3, C4, C5, C14, C15, C16, C17, C18, C19, C20, C21, C22, C23, C24, C25, C26, C27, C28, C29, C30, C31, C32, C33, C34, C35, C37, C38, C40, C41, C42, C43, C58, C67, C72, C73, C74, C77, C80, C82, C87, C88: 220n; C_0603
C6, C7, C8, C9, C10, C11, C12, C13, C84, C85, C86: 680p; C_0603
C36, C39: 12p; C_0603
C44, C49, C52, C53, C54, C55, C56, C59, C60, C61, C62, C64, C65, C66, C89: 10u; C_1206
C45, C46, C47, C48, C50, C79: 33n; C_0603
C51, C57, C63: 330u; c_elec_10x10.5
C68, C69, C70, C71: 100u; c_elec_493-3953-2-ND_6.3x7.7
D1: LM4040; SOT-23
D2, D3: 6V Zener; D_SOD-123
HS1, HS2: Heat_Sink; HeatSink
IC1: ATMEGA16M1-A; TQFP-32_7x7mm_Pitch0.8mm
ILTC1: 0; ILTC
J1: Conn_02x03_Odd_Even; PinHeader_2x03_P2.54mm_Vertical
J2: 4910SCK; TestPoint_Pad_D1.0mm
J3: 4910SDI; TestPoint_Pad_D1.0mm
J4: 4910SDO; TestPoint_Pad_D1.0mm
J5: 4910STR; TestPoint_Pad_1.0x1.0mm
J6: Conn_02x02_Top_Bottom; PinHeader_2x02_P2.54mm_Vertical
P1: CONN_6; ARDUINO-SIL-6
P2, P9, P10: CONN_8; ARDUINO-SIL-8
P3, P6, P7: CONN_01X04; Pin_A98335-ND_1x04
P4: CONN_01X03; PinHeader_1x03_P2.54mm_Vertical
P5: CONN_01X05; PinHeader_1x05_P2.54mm_Vertical
P8: CONN_9; SIL-9
P11: CONN_2; SIL-2
P12: CONN_01X03; 277-1722-ND
P14: CONN_01X03; Pin_Header_277-1578-ND_3x01
P15: CONN_01X03; Socket_Strip_Straight_1x03
Q1, Q2, Q3, Q4, Q5, Q6: IRF5406
R1, R2, R20, R29, R33, R34, R53, R61, R76, R77, R78, R79, R80, R81: 1.47k; R_0603
R3, R4, R5, R6, R7, R8, R9, R10, R21, R22: 56k; R_0603
R11, R12, R13, R14, R15, R16, R17, R18: 0.09; R_1206
R19, R25, R26, R27, R30, R31, R32: 1k; R_0603
R23, R39, R41, R42, R44, R46, R47, R48, R52, R64, R68, R70, R72: 47; R_0603
R24, R28, R35, R36, R37, R66: DNP; R_0603
R38, R57, R58: .005; R_1206
R40, R43, R45, R49, R50, R51: 470k; R_0603
R54, R55, R56, R59, R60, R63, R83: 1k; R_0603_1608Metric
R62, R65: DNP; R_0603_1608Metric
R67, R69, R71, R73, R74, R75: 24.3k; R_0603
R82, R84: 1.47k; R_0603_1608Metric
U1, U2, U3, U4: DRV8818
U5: A4910; A4910-LQFP_48
Y1: 16M; Crystal_SMD_2016-4pin_2.0x1.6mm

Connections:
+24V: C18.2, C20.2, C22.2, C24.2, C26.1, C27.1, C28.1, C29.1, C37.1, C38.1, C40.1, C51.1, C52.1, C53.1, C54.1, C55.1, C56.1, C57.1, C59.1, C60.1, C61.1, C62.1, C63.1, C64.1, C65.1, C66.1, C67.1, C68.1, C69.1, C70.1, C71.1, C88.1, C89.1, ILTC1.2, P11.1, P14.1, Q1.D, Q3.D, Q5.D, R55.2, R59.2, R60.2, U1.15 (VMB), U1.28 (VMA), U2.15 (VMB), U2.28 (VMA), U3.15 (VMB), U3.28 (VMA), U4.15 (VMB), U4.28 (VMA), U5.7 (VBB)
/2V5REF: D1.1 (+), R19.1, R56.2
/3V3: P2.4
/5V_LED: P5.2, R54.2
/24V_LED: P5.3, R55.1, R59.1, R60.1
/A0_STEP_X1_EN: IC1.31 ((PCINT24/OCD/~RESET~)PE0), P1.1, U1.27 (SLEEPn)
/A1_Stepper_PMode: P1.2, R83.1
/A2_LIMIT_X1: IC1.2 ((PCINT19/TXD/TXLIN/OC0A/~SS~/MOSI_A)PD3), P1.3, R82.1
/A3_64M1MISO: IC1.1 ((PCINT18/PSCIN2/OC1A/MISO_A)PD2), P1.4, R84.1
/A4_SPINDLE_OVERLOAD: IC1.7 ((PCINT11/T1/ICP1B/RXCAN)PC3), IC1.12 ((PCINT20/ADC1/RXD/RXLIN/ICP1A/SCK_A)PD4), P1.5
/A5_PROBE: C48.2, P1.6, R42.1
/A4910Fault: IC1.25 ((PCINT15/D2A/AMP2+)PC7), U5.17 (DIAG)
/AHI: IC1.29 ((PCINT16/PSCOUT0A)PD0), U5.18 (AHI)
/ALO: IC1.28 ((PCINT7/ADC4/SCK/PSCOUT0B)PB7), U5.19 (ALO)
/ARD_UNDEF: P2.1
/ARD_VIN: P2.8
/AVCC: C41.1, IC1.19 (AVCC), R23.2
/BHI: IC1.30 ((PCINT8/INT3/PSCOUT1A)PC0), U5.20 (BHI)
/BLAC_XTAL1: C36.2, IC1.10 ((PCINT25/OC0B/XTAL1)PE1), Y1.1
/BLAC_XTAL2: C39.1, IC1.11 ((PCINT26/ADC0/XTAL2)PE2), Y1.3
/BLAC_aRef: C79.2, IC1.21 (AREF(ISRC))
/BLDC_En: IC1.24 ((PCINT4/AMP0+)PB4), U5.12 (RESETn)
/BLO: IC1.27 ((PCINT6/ADC7/PSCOUT1B)PB6), U5.21 (BLO)
/CA: C45.1, U5.2 (CA)
/CB: C47.1, U5.45 (CB)
/CC: C46.1, U5.40 (CC)
/CHI: IC1.8 ((PCINT0/MISO/PSCOUT2A)PB0), U5.22 (CHI)
/CLO: IC1.9 ((PCINT1/MOSI/PSCOUT2B)PB1), U5.23 (CLO)
/CP1: C73.2, C74.2, U5.5 (CP1)
/CP2: C73.1, C74.1, U5.4 (CP2)
/CSAM: C84.2, R73.1, R77.2, U5.34 (CSAM)
/CSAP: C84.1, R67.1, R76.2, U5.33 (CSAP)
/CSBM: C85.2, R74.1, R79.2, U5.31 (CSBM)
/CSBP: C85.1, R69.1, R78.2, U5.30 (CSBP)
/CSCM: C86.2, R75.1, R81.2, U5.28 (CSCM)
/CSCP: C86.1, R71.1, R80.2, U5.27 (CSCP)
/CUR_A: IC1.15 ((PCINT23/ACMP0)PD7), IC1.26 ((PCINT5/ADC6/INT2/ACMPN1/AMP2-)PB5), R73.2, U5.35 (CSAO)
/CUR_B: IC1.18 ((PCINT13/ADC9/ACMP3/AMP1+)PC5), IC1.22 ((PCINT14/ADC10/ACMP1)PC6), R74.2, U5.32 (CSBO)
/CUR_C: IC1.13 ((PCINT21/ADC2/ACMP2)PD5), IC1.17 ((PCINT12/ADC8/ACMPN3/AMP1-)PC4), R75.2, U5.29 (CSCO)
/D2_STEP_X: P10.6, U1.19 (STEP), U2.19 (STEP)
/D3_STEP_Y: P10.5, U3.19 (STEP)
/D4_STEP_Z: P10.4, U4.19 (STEP)
/D5_DIR_X: P10.3, U1.3 (DIR), U2.3 (DIR)
/D6_DIR_Y: P10.2, U3.3 (DIR)
/D7_DIR_Z: P10.1, U4.3 (DIR)
/D8_STEP_EN_n: P9.8, U1.26 (ENABLEn), U2.26 (ENABLEn), U3.26 (ENABLEn), U4.26 (ENABLEn)
/D9_LIMIT_X2: C30.1, P9.7, R25.2
/D10_LIMIT_Y: C31.1, P9.6, R26.2
/D11_SPIN_PWM: P9.5, R21.2
/D12_LIMIT_Z: C32.1, P9.4, R27.2
/D13_SPIN_DIR: IC1.23 ((PCINT3/AMP0-)PB3), P9.3
/DECAY: C1.1, R1.2, R2.1, U1.5 (DECAY), U2.5 (DECAY), U3.5 (DECAY), U4.5 (DECAY)
/ESTOP_Filtered: C77.1, D2.1 (K), R64.2, U1.17 (RESETn), U2.17 (RESETn), U3.17 (RESETn), U4.17 (RESETn), U5.11 (COASTn)
/ESTOP_n: P15.2, R61.2, R64.1
/GHA: R39.1, U5.48 (GHA)
/GHAZ: Q1.G, R39.2, R40.2
/GHB: R44.1, U5.43 (GHB)
/GHBZ: Q3.G, R44.2, R45.2
/GHC: R48.1, U5.38 (GHC)
/GHCZ: Q5.G, R48.2, R49.2
/GLA: R41.1, U5.47 (GLA)
/GLAZ: Q2.G, R41.2, R43.1
/GLB: R46.1, U5.42 (GLB)
/GLBZ: Q4.G, R46.2, R50.1
/GLC: R47.1, U5.37 (GLC)
/GLCZ: Q6.G, R47.2, R51.1
/HALL_A: IC1.6 ((PCINT10/T0/TXCAN)PC2), IC1.32 ((PCINT17/CLKO/PSCIN0)PD1), J1.6, R29.2
/HALL_B: IC1.3 ((PCINT9/PSCIN1/OC1B/~SS_A~)PC1), J1.4, R33.2
/HALL_C: J1.2, R34.2, R84.2
/IOREF: P2.2
/ISET_A: R24.1, R67.2, R68.2
/ISET_B: R28.1, R69.2, R70.2
/ISET_C: R66.1, R71.2, R72.2
/LSSA: C54.2, C66.2, Q2.S, R38.2, R43.2, R76.1, U5.46 (LSSA)
/LSSB: C53.2, C65.2, Q4.S, R50.2, R57.2, R78.1, U5.41 (LSSB)
/LSSC: C59.2, C60.2, Q6.S, R51.2, R58.2, R80.1, U5.36 (LSSC)
/PHASE_A: C45.2, P12.1, Q1.S, Q2.D, R40.1, U5.1 (SA)
/PHASE_B: C47.2, P12.2, Q3.S, Q4.D, R45.1, U5.44 (SB)
/PHASE_C: C46.2, P12.3, Q5.S, Q6.D, R49.1, U5.39 (SC)
/PI_PRB: C50.2, R42.2, R52.1
/PI_X2LIM: C33.1, R25.1, R30.2
/PI_YLIM: C34.1, R26.1, R31.2
/PI_ZLIM: C35.1, R27.1, R32.2
/PROBE_NOISY: P5.1, R52.2, R53.2
/RESET_328p: D2.2 (A), P2.3
/SPIN_PWM_to_Analog: C87.2, IC1.16 ((PCINT2/ADC5/INT1/ACMPN0)PB2), R21.1, R22.1
/Spindle_Wiper: J1.3, P5.5, R62.2
/VBRG: ILTC1.1, U5.8 (VBRG)
/VREF_DIV: R20.1, R63.2
/VREF_Steppers: C72.1, R19.2, R63.1, R83.2, U1.8 (VREF), U2.8 (VREF), U3.8 (VREF), U4.8 (VREF)
/VREG: C43.1, C44.1, U5.3 (VREG)
/X1LIM: P4.2, R65.1, R82.2
/X1_A1: P6.1, U1.4 (AOUT1)
/X1_A2: P6.2, U1.25 (AOUT2)
/X1_B1: P6.3, U1.11 (BOUT1)
/X1_B2: P6.4, U1.18 (BOUT2)
/X1_CP1: C19.1, U1.23 (CP1)
/X1_CP2: C19.2, U1.24 (CP2)
/X1_ISENA: R15.1, U1.1 (ISENA)
/X1_ISENB: R11.1, U1.14 (ISENB)
/X1_RCA: C6.1, R3.1, U1.6 (RCA)
/X1_RCB: C10.1, R7.1, U1.9 (RCB)
/X1_VCP: C18.1, U1.22 (VCP)
/X1_VGD: C14.1, U1.20 (VGD)
/X2LIM: P8.8, R30.1, R35.1
/X2_A1: P7.1, U2.4 (AOUT1)
/X2_A2: P7.2, U2.25 (AOUT2)
/X2_B1: P7.3, U2.11 (BOUT1)
/X2_B2: P7.4, U2.18 (BOUT2)
/X2_CP1: C21.1, U2.23 (CP1)
/X2_CP2: C21.2, U2.24 (CP2)
/X2_ISENA: R16.1, U2.1 (ISENA)
/X2_ISENB: R12.1, U2.14 (ISENB)
/X2_RCA: C7.1, R4.1, U2.6 (RCA)
/X2_RCB: C11.1, R8.1, U2.9 (RCB)
/X2_VCP: C20.1, U2.22 (VCP)
/X2_VGD: C15.1, U2.20 (VGD)
/YLIM: P8.5, R31.1, R36.1
/Y_A1: P3.1, U3.4 (AOUT1)
/Y_A2: P3.2, U3.25 (AOUT2)
/Y_B1: P3.3, U3.11 (BOUT1)
/Y_B2: P3.4, U3.18 (BOUT2)
/Y_CP1: C23.1, U3.23 (CP1)
/Y_CP2: C23.2, U3.24 (CP2)
/Y_ISENA: R17.1, U3.1 (ISENA)
/Y_ISENB: R13.1, U3.14 (ISENB)
/Y_RCA: C8.1, R5.1, U3.6 (RCA)
/Y_RCB: C12.1, R9.1, U3.9 (RCB)
/Y_VCP: C22.1, U3.22 (VCP)
/Y_VGD: C16.1, U3.20 (VGD)
/ZLIM: P8.2, R32.1, R37.1
/Z_A1: J6.1, U4.4 (AOUT1)
/Z_A2: J6.2, U4.25 (AOUT2)
/Z_B1: J6.3, U4.11 (BOUT1)
/Z_B2: J6.4, U4.18 (BOUT2)
/Z_CP1: C25.1, U4.23 (CP1)
/Z_CP2: C25.2, U4.24 (CP2)
/Z_ISENA: R18.1, U4.1 (ISENA)
/Z_ISENB: R14.1, U4.14 (ISENB)
/Z_RCA: C9.1, R6.1, U4.6 (RCA)
/Z_RCB: C13.1, R10.1, U4.9 (RCB)
/Z_VCP: C24.1, U4.22 (VCP)
/Z_VGD: C17.1, U4.20 (VGD)
/a4910_SCK: J2.1, U5.14 (SCK)
/a4910_SDI: J3.1, U5.15 (SDI)
/a4910_SDO: J4.1, U5.16 (SDO)
/a4910_STRn: J5.1, U5.13 (STRn)
GND: C1.2, C2.2, C3.2, C4.2, C5.2, C6.2, C7.2, C8.2, C9.2, C10.2, C11.2, C12.2, C13.2, C14.2, C15.2, C16.2, C17.2, C26.2, C27.2, C28.2, C29.2, C30.2, C31.2, C32.2, C33.2, C34.2, C35.2, C36.1, C37.2, C38.2, C39.2, C40.2, C41.2, C42.2, C43.2, C44.2, C48.1, C49.2, C50.1, C51.2, C52.2, C55.2, C56.2, C57.2, C58.2, C61.2, C62.2, C63.2, C64.2, C67.2, C68.2, C69.2, C70.2, C71.2, C72.2, C77.2, C79.1, C80.2, C82.2, C87.1, C88.2, C89.2, D1.2 (-), D3.2 (A), HS1.1, HS1.2, HS2.1, HS2.2, IC1.5 (GND), IC1.20 (AGND), J1.1, P2.6, P2.7, P4.3, P5.4, P8.3, P8.6, P8.9, P9.2, P11.2 (PM), P14.2, P14.3, P15.3, R2.2, R3.2, R4.2, R5.2, R6.2, R7.2, R8.2, R9.2, R10.2, R11.2, R12.2, R13.2, R14.2, R15.2, R16.2, R17.2, R18.2, R20.2, R22.2, R38.1, R57.1, R58.1, R61.1, R62.1, R68.1, R70.1, R72.1, R77.1, R79.1, R81.1, U1.7 (GND), U1.16 (SRn), U1.21 (GND), U1.29 (GND(PAD)), U2.7 (GND), U2.16 (SRn), U2.21 (GND), U2.29 (GND(PAD)), U3.7 (GND), U3.16 (SRn), U3.21 (GND), U3.29 (GND(PAD)), U4.7 (GND), U4.16 (SRn), U4.21 (GND), U4.29 (GND(PAD)), U5.6 (PGND), U5.9 (AGND), U5.24 (OPAP), U5.25 (OPAM), U5.49 (PAD), Y1.2, Y1.4
VCC: C2.1, C3.1, C4.1, C5.1, C42.1, C49.1, C58.1, C80.1, C82.1, D3.1 (K), IC1.4 (VCC), J1.5, P2.5, P4.1, P8.1, P8.4, P8.7, P15.1, R1.1, R23.1, R24.2, R28.2, R29.1, R33.1, R34.1, R35.2, R36.2, R37.2, R53.1, R54.1, R56.1, R65.2, R66.2, U1.10 (VCC), U1.12 (USM1), U1.13 (USM0), U2.10 (VCC), U2.12 (USM1), U2.13 (USM0), U2.27 (SLEEPn), U3.10 (VCC), U3.12 (USM1), U3.13 (USM0), U3.27 (SLEEPn), U4.10 (VCC), U4.12 (USM1), U4.13 (USM0), U4.27 (SLEEPn), U5.10 (VDD)

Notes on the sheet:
VCC ZLIM GND VCC YLIM GND VCC X2LIM GND
ARDUINO BOTTOM RIGHT
ARDUINO TOP RIGHT
ARDUINO BOTTOM LEFT
FAN
PH_A PH_B PH_C
24V GND
BLDC PHASE
BLDC HALL
24Vin PGND CHASSIS GND
X1-RIGHT
X2-LEFT
blue yellow green
yellow green blue
VCC ESTOP GND
Comparator inputs
PSC inputs
PSC outputs
firmware update process: -(temp) write SPI firmware to 328p -bitbanging new 64M1 firmware -write grbl firmware back to 328p
Counter
13 Hz LPF
goalRPM
Spindle Direction
Direction
grbl: slow down
328p Output: L: Steppers Low power (VREF=1.04v) - Steppers Idle Z: Steppers Med power (VREF=1.78v) - Normal Motion H: Steppers High power (VREF=3.12v) - USE SPARINGLY!
Probe_LED 5V_LED 24V_LED GND_LED Spindle_LED
VCC SPINDLE GND
H_A H_B H_C
64M1_MOSI
64M1_CLK
2x2 so physical connector fits through bushings
64M1_MISO
64M1_RST
VCC X1LIM GND
Filter not required on X1; Only used during Autolevel
LO: Motion Disabled HI: Normal Operation
ARDUINO TOP LEFT

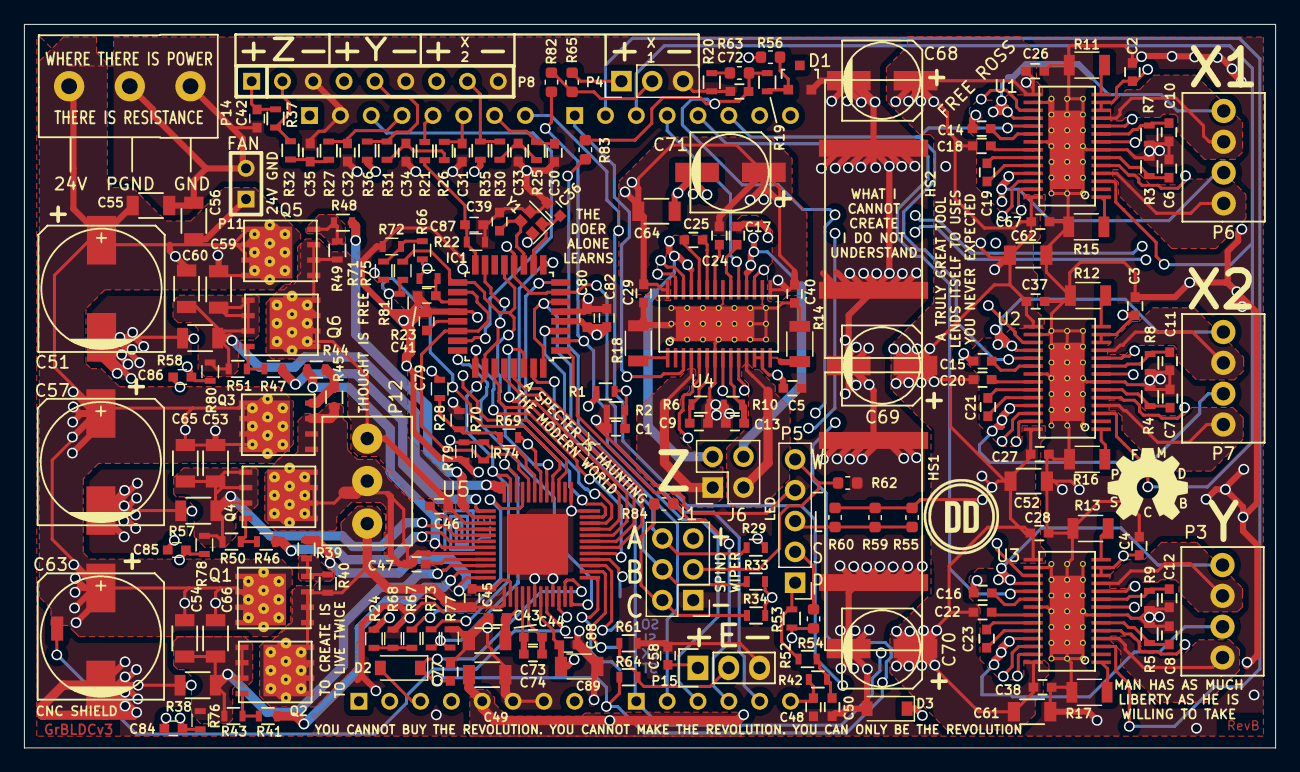
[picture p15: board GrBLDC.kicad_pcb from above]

Board: 6 copper layers, 103.1 x 59.6 mm, 207 parts (0 on the bottom side), 145 nets.

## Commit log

2020-01-06 Initial Upload
    PCB is complete. This is the shipping version.
    [2 - BOM - with P&P.ods, 3 - GrBLDC3v1.csv, GrBLDC-2019-10-30-12-31-24.sch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]
2020-01-23 Changed opamp gain offset
    opamp offset functionality (i.e. 0A = 8- mV) made gain non-uniform. Removed opamp offset entirely, as we don't really need it, and I'd rather integrate current more linearly.
    [GrBLDC.kicad_pcb, GrBLDC.sch]
2021-12-14 Added latest version and cleaned up
    [2 - BOM - with P&P.ods, 3 - GrBLDC3v1-AS FOUND.csv, 3 - GrBLDC3v1.csv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]
2021-12-14 Deleted Large Files
    [combined.drl, combined.gbl, combined.gbs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]
